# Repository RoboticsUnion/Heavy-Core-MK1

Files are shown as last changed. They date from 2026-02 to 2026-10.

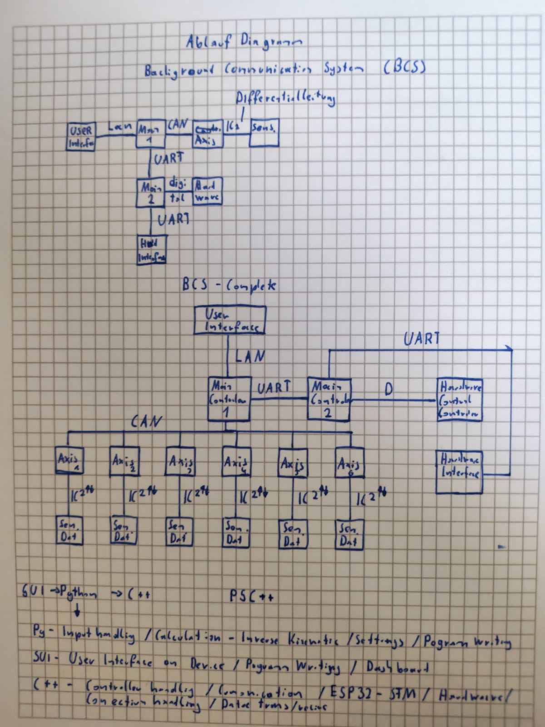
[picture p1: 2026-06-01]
electronic _engineering/BackgroundCommunicationSystem_ConceptDrwing.JPEG

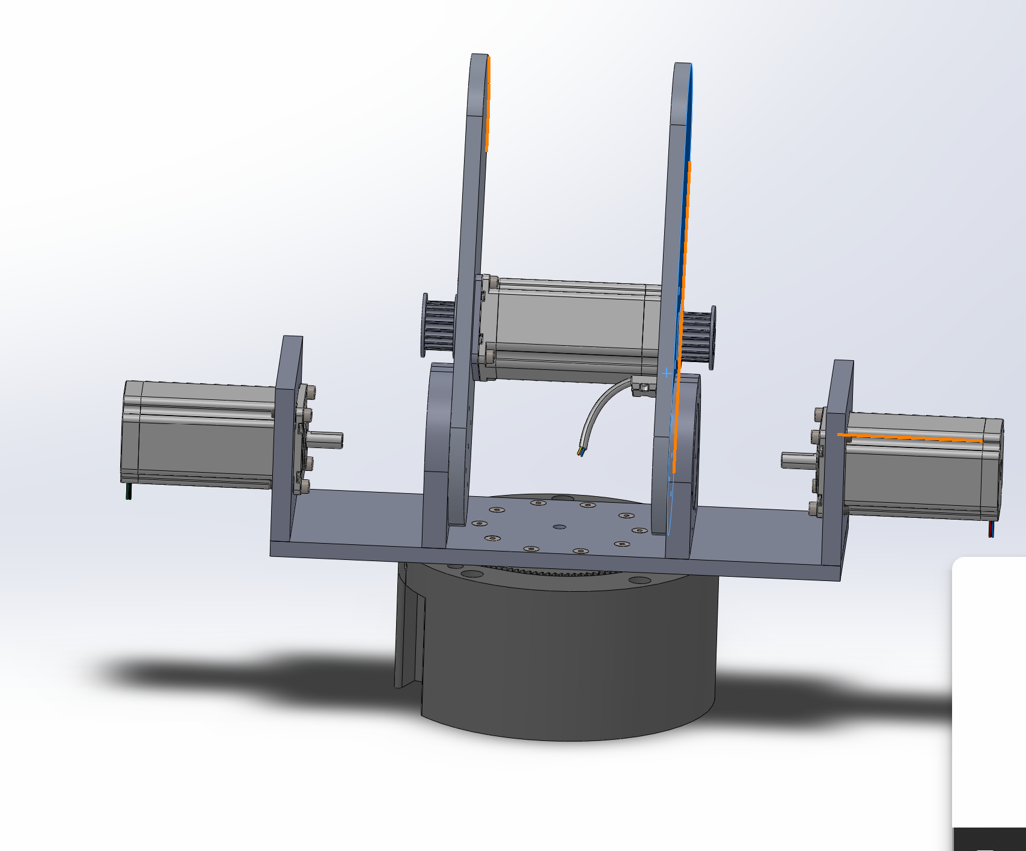
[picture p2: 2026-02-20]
docs/Images/ArmAssmb_Img1.png

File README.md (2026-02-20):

# Heavy-Core-MK1
Heavy-Core-MK1 is the development of a modular robotic arm platform.
The goal is to create a scalable, affordable robotics ecosystem where hardware and software are engineered together from the ground up.

The first two axes have already been designed, printed, assembled, and successfully tested. In parallel,
we are developing our own control software for precise motion control.

# Our Vision:

We aim to build a 6 DOF robitic arm that:
  - Is upgradeable with interchangeable end-effectors
  - Is structurally optimized for strength-to-weight efficiency
  - Includes a custom-developed control software
  - Allows future automation features
  - Serves as a platform for robotics development

# Custom Control Software

Our robotic arm will not rely solely on position control.
We are developing a control application that will include: 
  - Real-Time position feedback
  - Inverse kinematics calculations
  - Intuitive controls
  - Integrated arm simulation to prevent collisions or overload situations
  - Expandable architecture for future features

# Current Development Status

Completed:
  - Torque calculations
  - CAD design of Axis 1 and 2
  - Stepper motor integration
  - First tests of the custom designed Gearboxes
  - Functional test of both Axis

In Progress:
  - Development of remaining Axis
  - Gearbox optimization
  - Software development
  - Control hardware integration

# Preliminary Technical Specifications
- Target DOF: 6 DOF
- currently functional: 2 DOF
- Actuators: Stepper motors
- Structure: Aluminum & PLA (Stronger 3D-printed material planned)
- Control system: Arduino & ESP32 based
- Sofware: Custom standalone desktop or mobile application

# Development Roadmap

| Phase | Description | Target |

| MK1 Alpha | 2 DOF mechanical validation, first project showcase | Completed |

| MK1 Beta | 4-6 DOF mechanical prototype | Q3 2026 (estimated) |

| MK1 Software Alpha | Basic motion control & UI | Q3 2026 |

| MK1 Integrated Demo | Hardware + software functional for demonstration | Q1 2027 (January, HTL Open house) |

| MK1 Full Prototype | Fully functional 6 DOF with software improvements | Post Open House (future milestone) |

# Why this project stands out

Heavy-Core is more than a 3D-printed robotic arm.
It is the foundation for a modular robotics ecosystem that is mostly custom designed.

Mechanical engineering, electronics and software development are 
combined in one unified system, driven by the abition and passion of young engineers.

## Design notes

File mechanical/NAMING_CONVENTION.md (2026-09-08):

# CAD-Files Naming Convention

Each CAD-File is named according to our Naming Convention. This allows us to have relativly compact, but meaningfull names.

NamingCon_Example

The file name contains following components:
   - the project name,
   - the subassembly, the file is contained in,
   - a rising part number, starting at 001 for every subassembly (not used for assemblies),
   - the category of the part,
   - the version number

NOTE: In some cases it is possible to put a small clarification (1-2 words) between the part category and version number

# List of available abbreviations

  Project Name:
  - HC1 = HeavyCore MK1 

  Subassembly:
  - BA = Base
  - SH = Shoulder
  - EB = Elbow
  - UPA = Upper arm
  - WR = Wrist
  - GRP = Gripper
  
  Part Category:
  - MT = Mount
  - GR = Gear
  - PLT = Plate
  - SPC = Spacer
  - PIN = Pin
  - HUB = Hub
  - SHAFT = Shaft
  - BRCKT = Bracket

  Exeptions:
  - CM = Common ( this is used for parts that are contained in several subassemblies, but are created for this project and not sourced from outside)
  - ASM = Assembly

# Clarifications

- Plate = mostly used for flat plates that are used as structural elements.
- Mount = used for parts that hold, support, or attach components in place.
- Bracket = used for structural parts that are used to connect, support, or secure components, often at an angle.

Not every subassembly that may be contained in this project has its own abreviation. The prject is divided into 6 subassemblies, one for each axis,
and the common folder, wich is a bit of an exeption. Smaller subassemblies within one of the declared subassemblies must not be specificly labeled in the file names.
However, a new folder can be created to organize files.

NamingCon_Example1

Example Assembly File Name:

NamingCon_Example2

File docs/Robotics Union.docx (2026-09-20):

Robotics Union

Junior Company David Dovjak, Eder Samuel

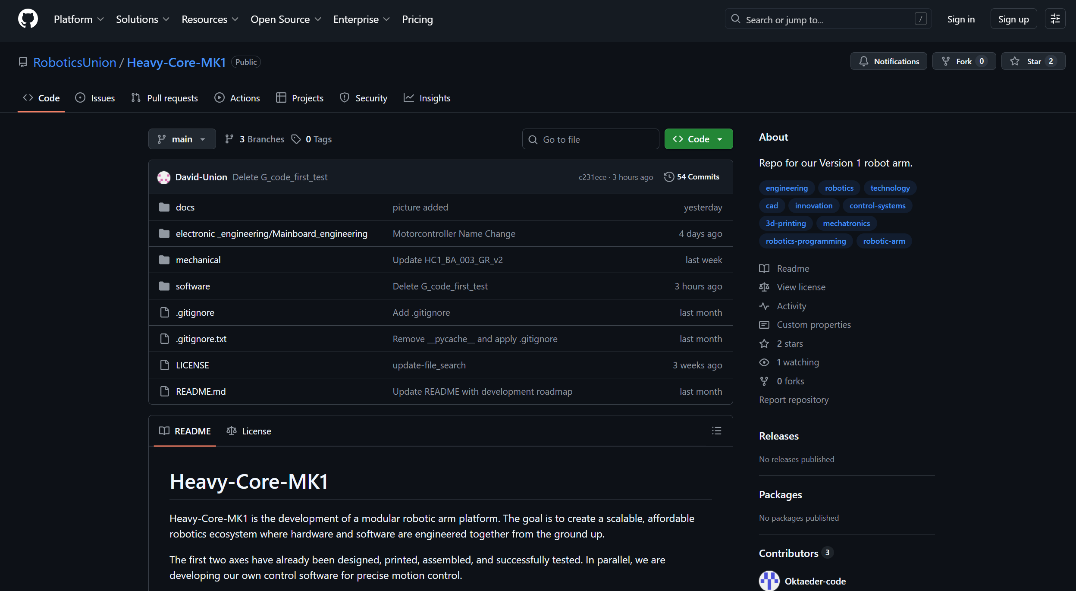
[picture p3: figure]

GitHub

Unser Hauptprojekt kann unter folgendem Link auf GitHub geöffnet werden: GitHub (https://github.com/RoboticsUnion/Heavy-Core-MK1)

Auf GitHub werden unsere Bauteile und Codes täglich geupdatet und ausgearbeitet. Dort gibt es auch direkt eine Übersicht, bzw. kann der Code getestet und die Bauteile als CAD-Datei geöffnet werden.

Code:

Der Code wird in C++ und Python geschrieben.

Bauteile:

Die Bauteile wurden in Fusion bearbeitet und seit neusten wechselten wir auf SolidWorks

Aufteilung:

David Dovjak – Code, Elektronik und Konstruktion der Werkzeugwechselstation

Eder Samuel – Konstruktion des Roboter Armes, Berechnung

GitHub Übersicht (siehe Link)

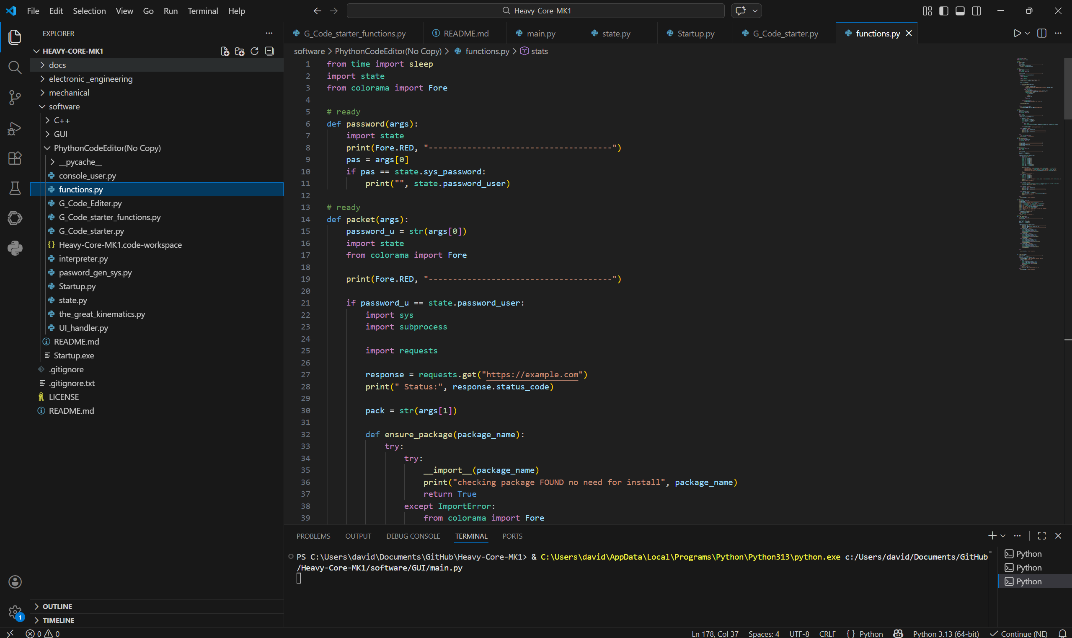
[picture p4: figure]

VS – Visual Studio Code

Alle Programme werden in Visual Studio Code geschrieben und bearbeitet. Python Code in der frontend und im backend; der C++ Teil ist für die Steuerung der Microcontroller. Vorher wurde in Py Charm gearbeitet, aber durch bessere Bearbeitungsmöglichkeiten haben wir auf VS gewechselt.

VS (Visual Studio Code): Ausschnitt der Programmierung

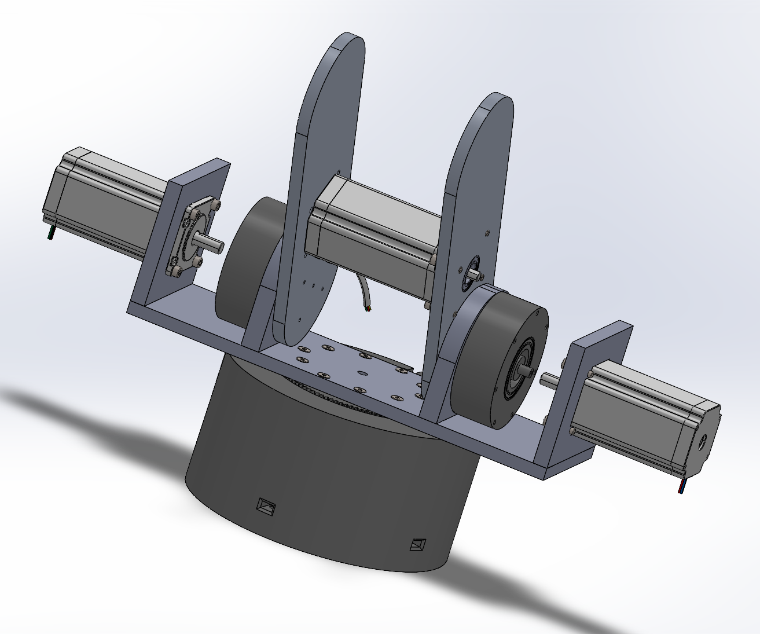
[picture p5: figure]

Konstruktion

CAD-Baugruppe des Roboterarmes (derzeitiger Stand)

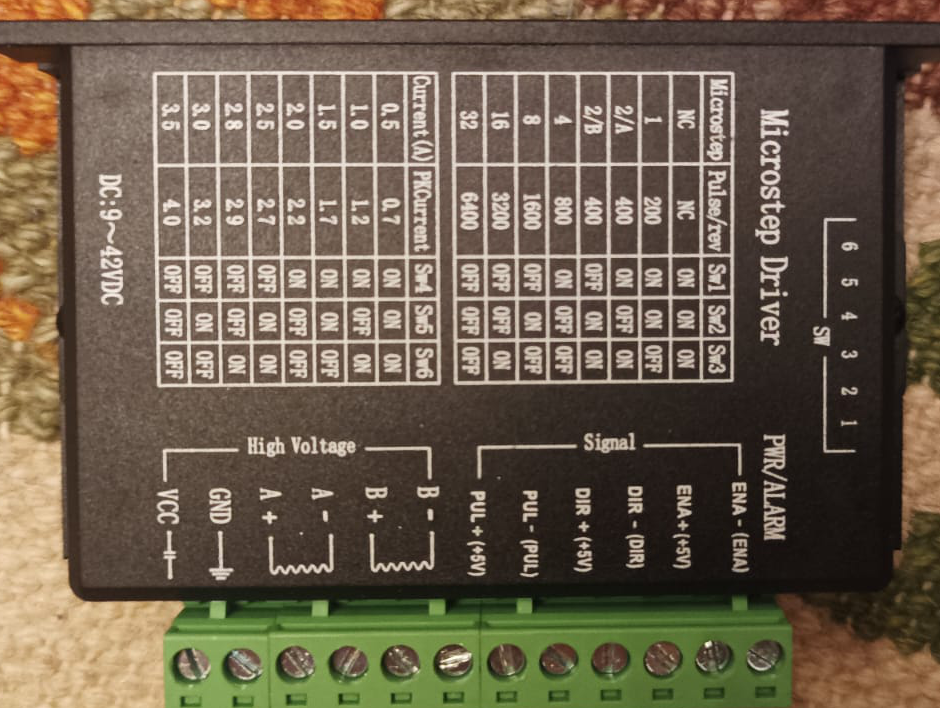
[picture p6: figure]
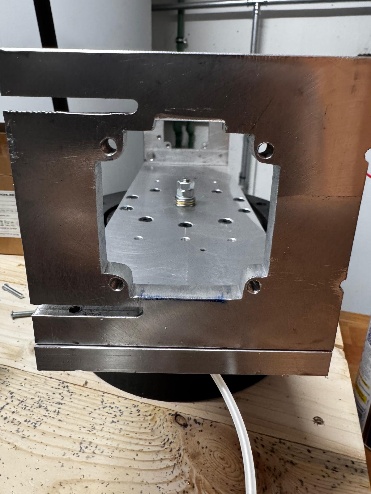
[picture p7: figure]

Motorcontroller TB6600

Aufbau: Motorhalterung 2. Achse

Aktueller Stand

Aktuell sind die ersten 2 Achsen fertig konstruiert, sowie selbst gefräst und zusammengebaut. Es wird gerade an der 3. Achse mit Riemenantrieb gearbeitet. Im fertigen Zustand soll der Roboterarm 6 Achsen haben, und einen Tool-Kopf der in x- und y-Richtung bewegt werden kann. Wir wollen damit einen Roboter bauen, der alle Aufgaben in der Industrie erledigen kann.

Der Arm hat eine maximale Hebekraft von bis zu circa 4 kg und durch unsere eigens erfundene Steuerung sollte er eine genaue und präzise Ausführung haben.

Getriebe:

Eigens designte cycloiden Getriebe, die eine starke Übersetzung liefern.

Motoren:

Wir verwenden Stepper Motoren der Ausführung Nema 17 und Nema 12 die mit einen TB6600 angesteuert werden.

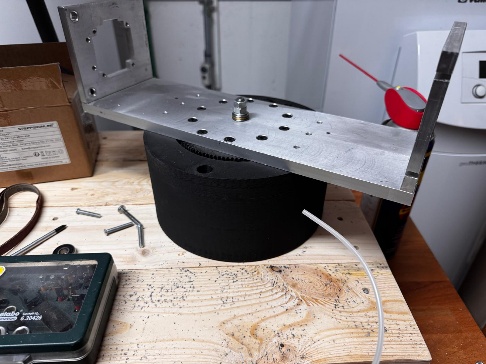
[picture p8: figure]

Aufbau: 1. und 2. Achse

Ziele

Wir haben bis jetzt schon ein großes Ziel erledigt: wir wurden seit Anfang des Projektes finanziell und logisch unterstützt, deswegen stellten wir am Infotag der HTBLVA Ferlach unseren Roboterarm aus und wir bekamen sehr viel gutes Feedback.

Für die Zukunft:

Fertigstellung des Armes in der Software SolidWorks und herstellen der benötigten Teile aus Aluminium und gehärtetem PLA für 3D-Drucker.

Software Fertigstellung GUI-Oberfläche des Hauptprogrammes. Dazu werden wir in Zukunft eine Kamera und einen LiDAR Sensor anbauen. Die zwei Komponenten werden von KI verarbeitet und es werden dann Funktionen zur Verfügung gestellt werden das per KI-Funktionen wie „Nimm den Blauen Würfel und lege ihn auf die Blau Fläche“ ausgeführt werden können.

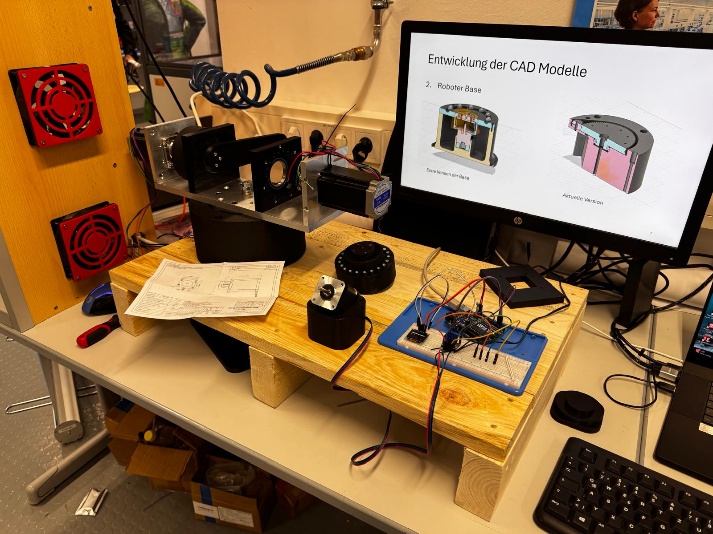
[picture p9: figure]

Auststellung am Infotag der HTBLVA Ferlach

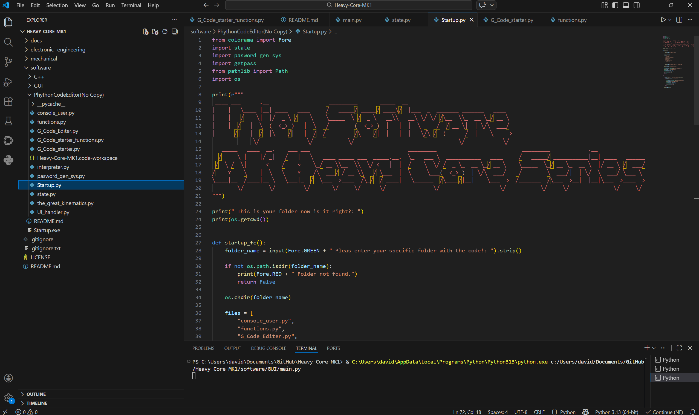
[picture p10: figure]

VS (Visual Studio Code): Ausschnitt der Programmierung

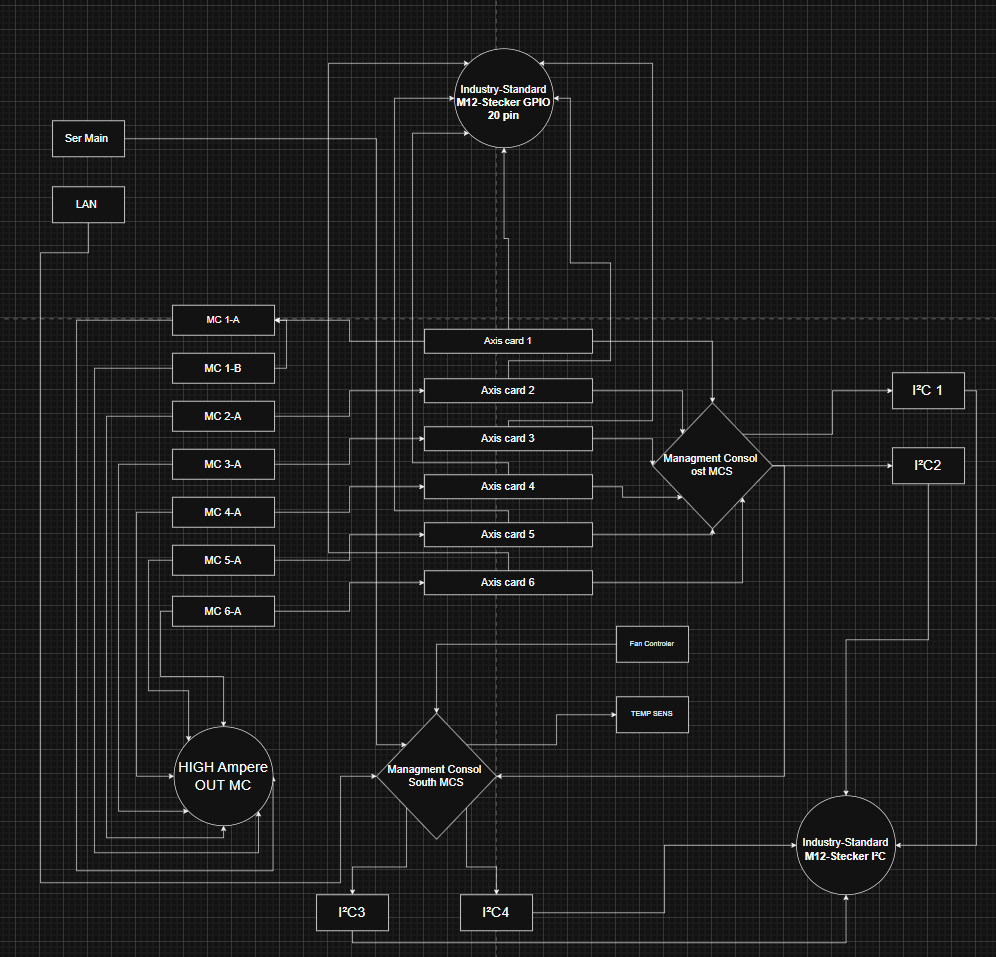
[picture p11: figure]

Logischer Aufbau von der Steuerungseinheit

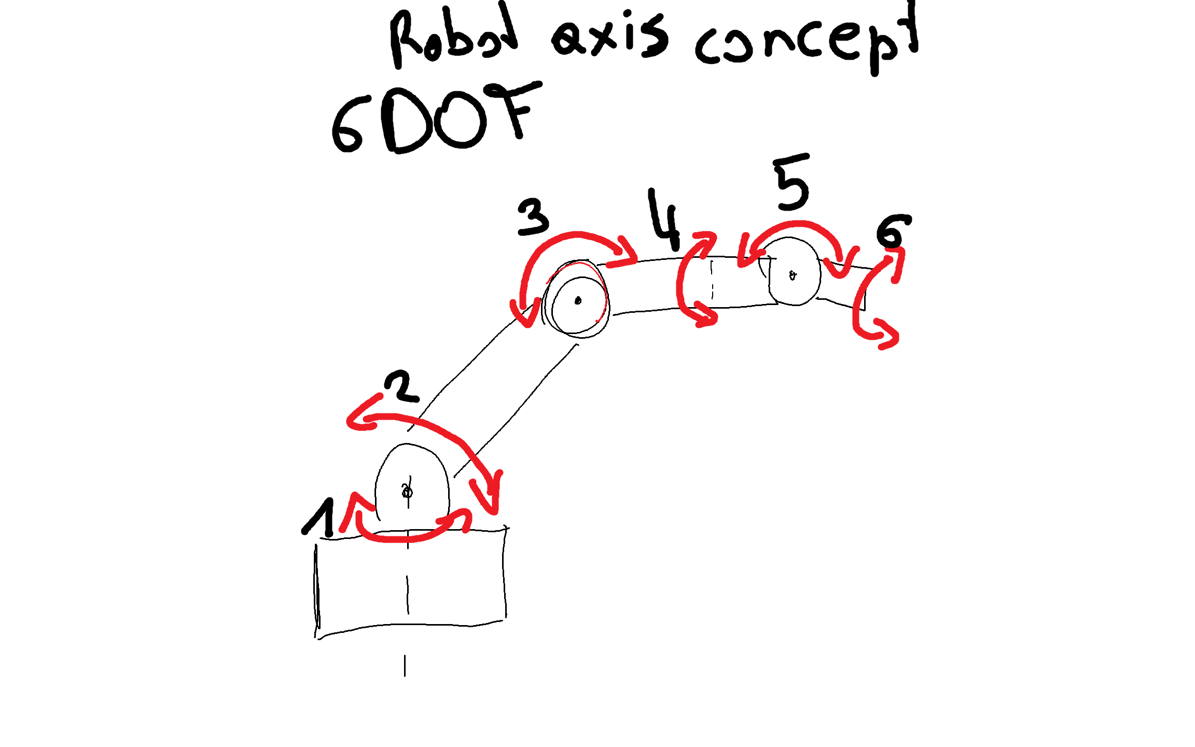
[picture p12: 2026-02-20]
docs/drawings/RobotAxisConcept.png

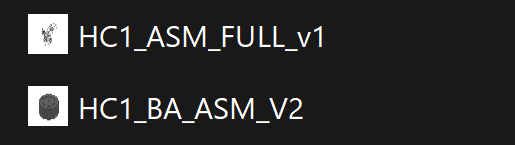
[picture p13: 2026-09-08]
docs/Images/NamingCon_Example2.png

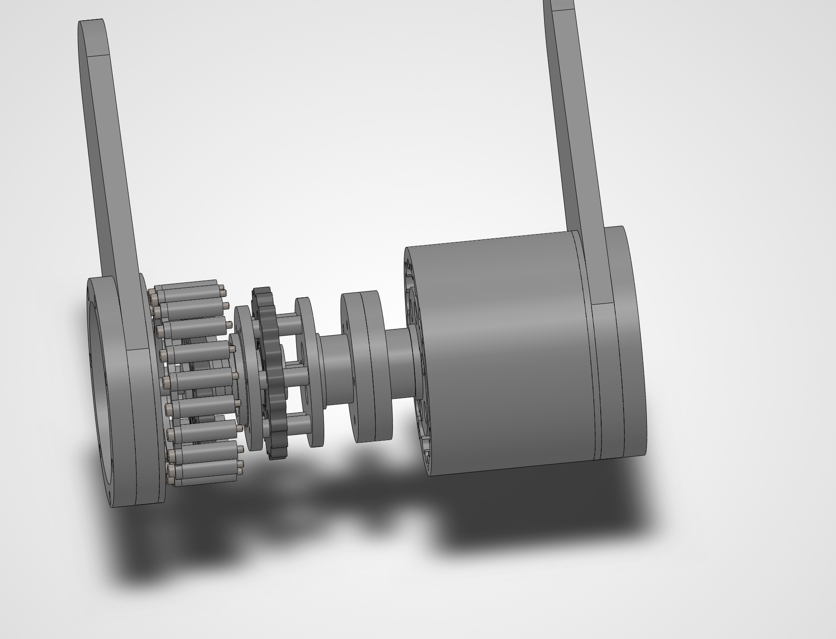
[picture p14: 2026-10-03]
docs/Images/Screenshot 2026-10-02 091949.png

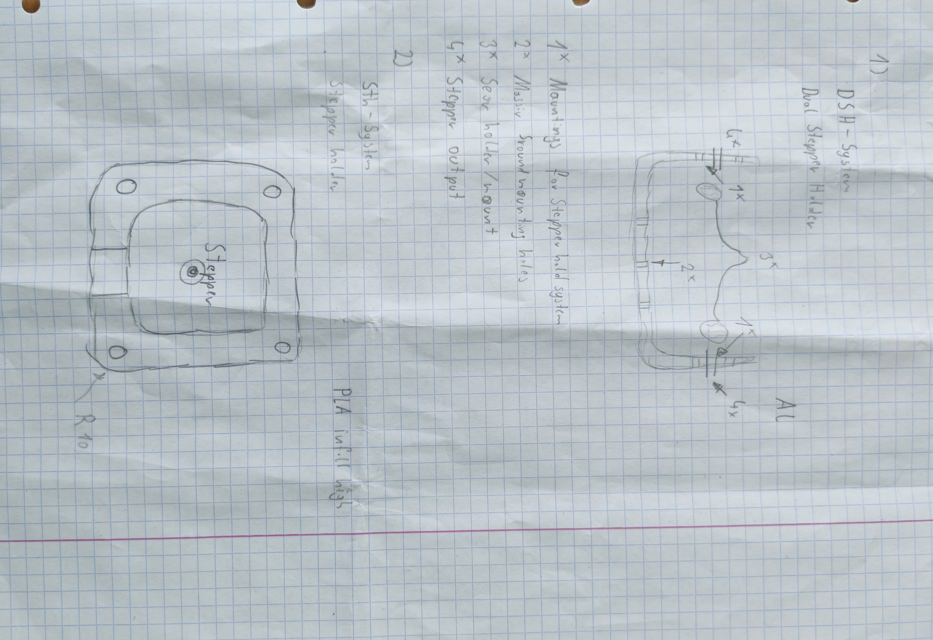
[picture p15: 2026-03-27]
docs/drawings/IMG_20260327_110558_edit_99301896493837.jpg

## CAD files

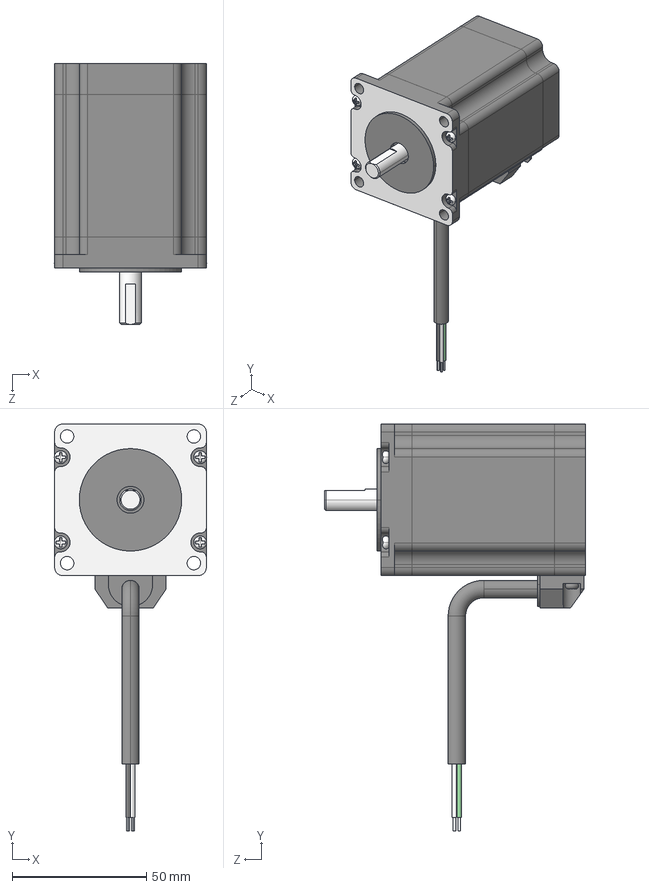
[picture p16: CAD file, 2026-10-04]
mechanical/assets/steppermotor/23HS30-2694S-Nema23SingleS_1.85nm.STEP
56.7 x 151.4 x 97.0 mm

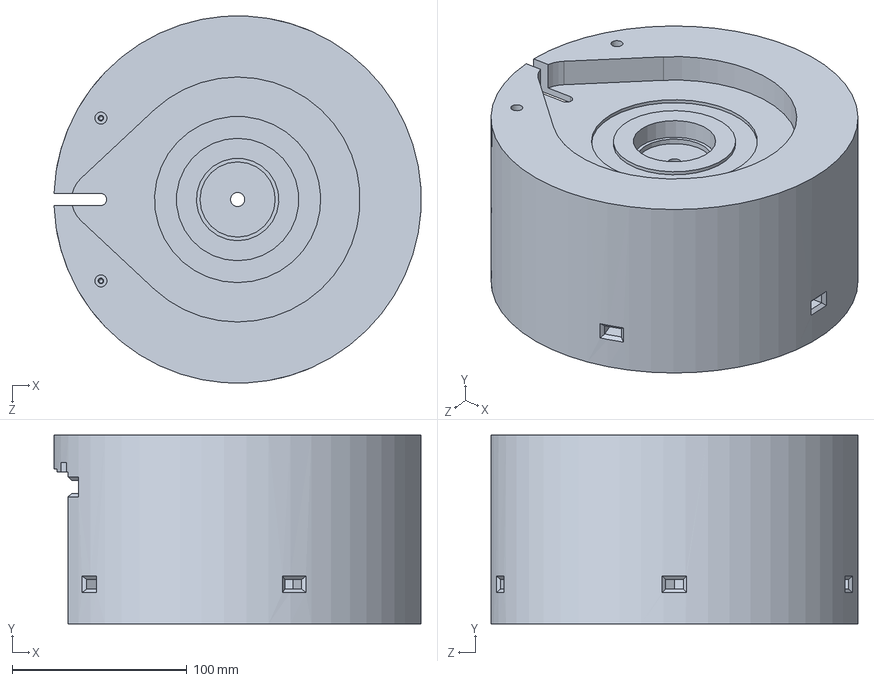
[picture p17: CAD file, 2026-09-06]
mechanical/cad/base/HC1_BA_001_MT_v2.SLDPRT
209.7 x 108.0 x 209.8 mm

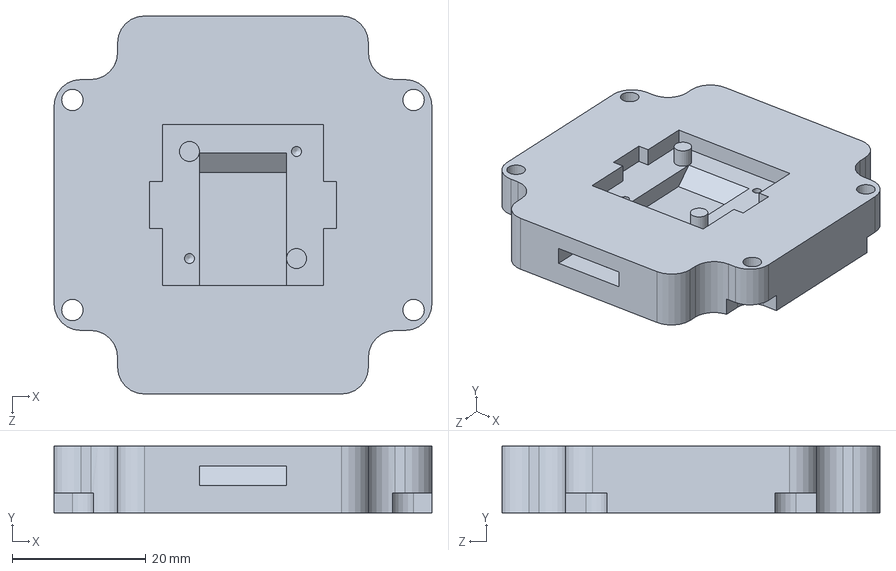
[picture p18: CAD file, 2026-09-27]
mechanical/cad/common/encoder_mounts/HC1_CM_001_MT_ENCODER_Nema23_v1.SLDPRT
56.5 x 10.0 x 56.5 mm

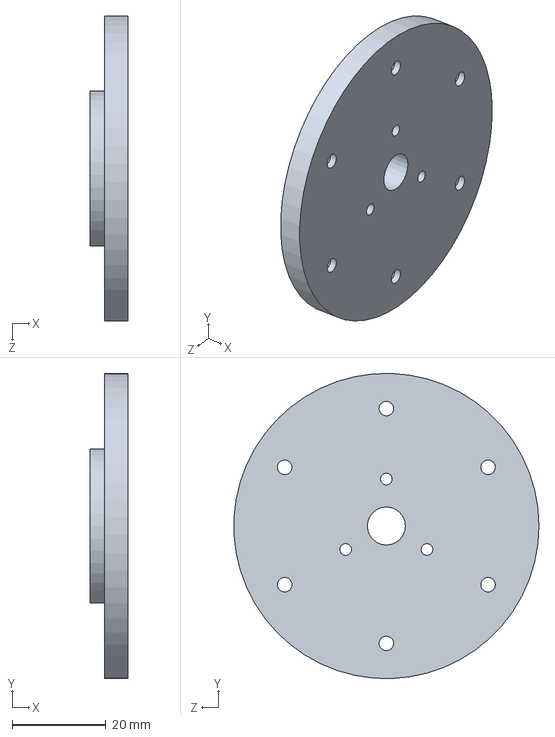
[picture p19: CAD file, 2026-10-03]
mechanical/cad/ellbow/CycloidalDrive/HC1_EB_005_MT_staticPins_v2.SLDPRT
8.00 x 65.0 x 64.9 mm

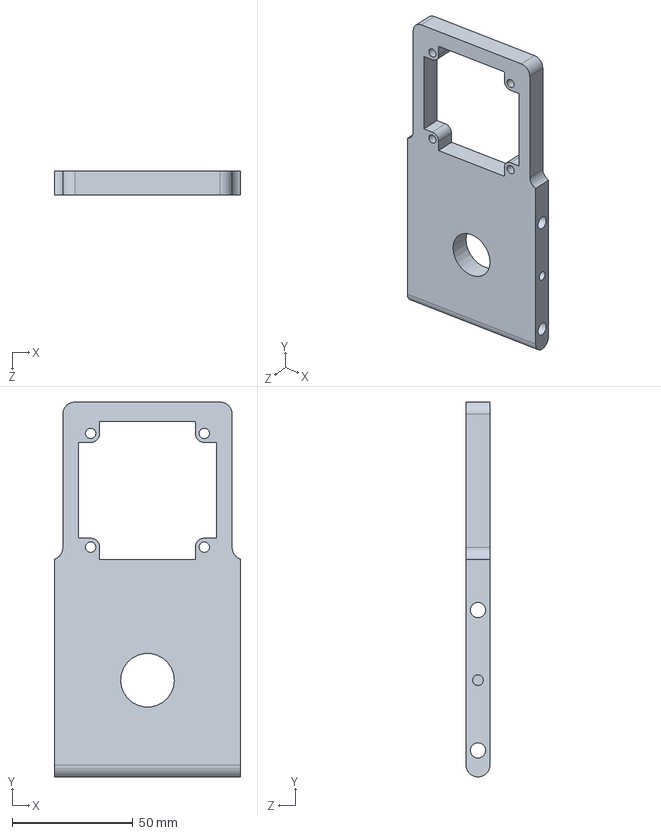
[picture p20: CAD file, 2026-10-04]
mechanical/cad/ellbow/HC_EB_13_MT_stepper_v1.SLDPRT
77.0 x 155.0 x 10.0 mm

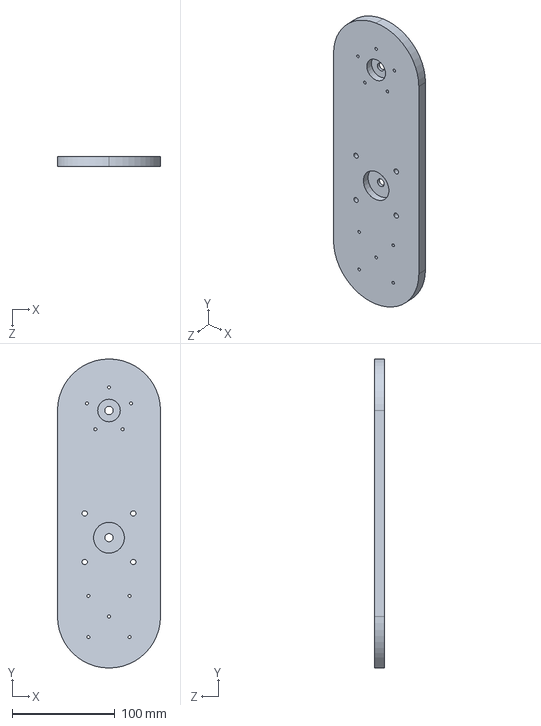
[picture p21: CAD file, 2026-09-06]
mechanical/cad/shoulder/HC1_SH_006_PLT_Axis_v1.SLDPRT
100.0 x 300.0 x 10.0 mm

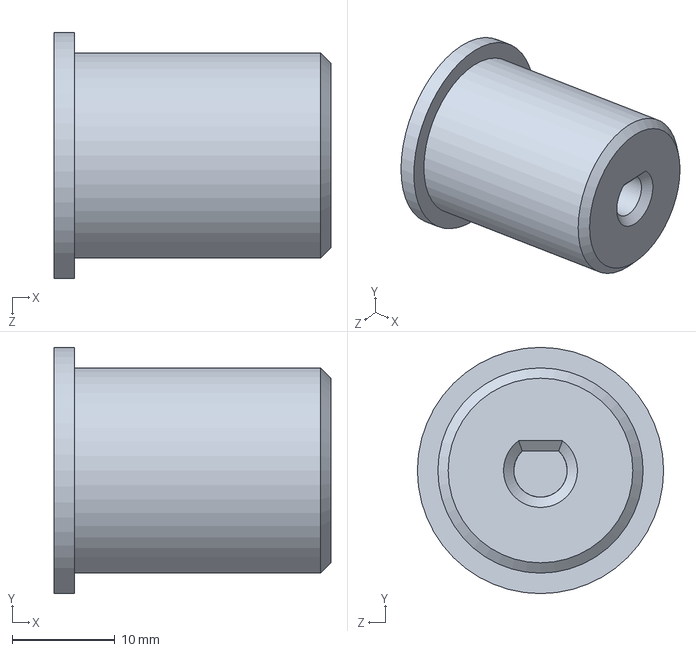
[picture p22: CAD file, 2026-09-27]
mechanical/cad/test_dev_parts/Cycloidal_input_Nema17.SLDPRT
27.0 x 24.0 x 24.0 mm

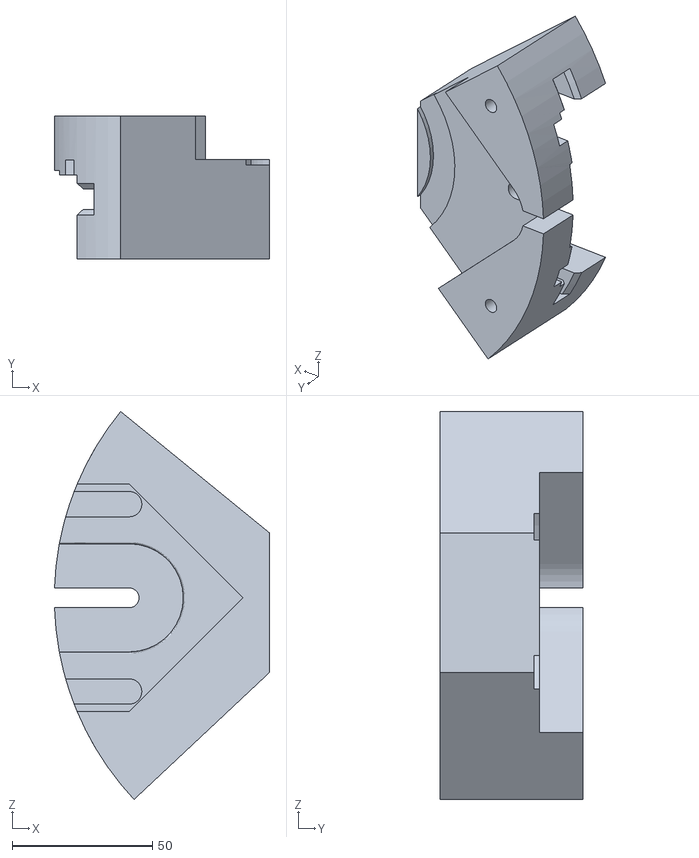
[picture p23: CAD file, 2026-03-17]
mechanical/stl/base/HC1_BA_001_MT_Ausschnitt.STL
76.6 x 51.0 x 138.2

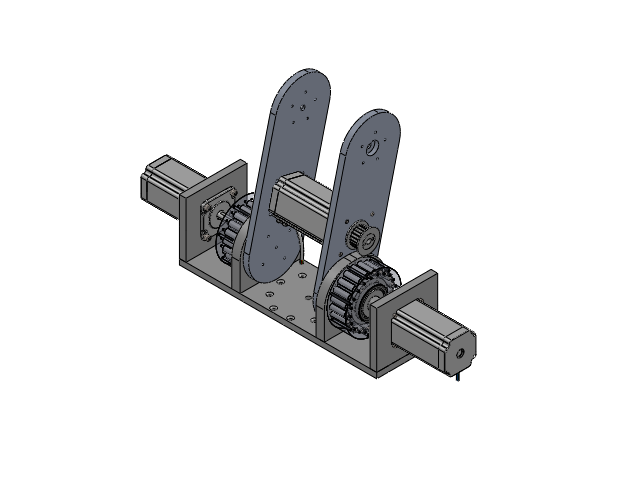
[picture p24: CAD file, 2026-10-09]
mechanical/assemblies/HC1_SH_ASM_v1.SLDASM
HC1_SH_001_PLT_v1
HC1_SH_002_MT_Motor_v1 x 2
HC1_SH_003_MT_Gearbox_v2 x 2
23HE45-4204S-Nema23SingleS.step x 2
69032RS Inner ring.stp x 2
69032RS Outer ring.stp x 2
69032RS Ball.stp x 22
69032RS Seal.stp x 4
6808ZZ Inner ring.stp x 2
6808ZZ Outer ring.stp x 2
6808ZZ Ball.stp x 42
6808ZZ Shield.stp x 4
HC1_SH_006_PLT_Axis_v1 x 2
HC1_SH_007_SPC_Motor_v1
HTD5M-Pully-20t x 2
HTD5M-Pully-20t-BeltGuard x 4
socket_head_cap_screw_M5x20 x 12
HC1_SH_008_MT_housing_v1 x 2
HC1_SH_011_PIN_static_v1 x 42
socket head cap screw_iso x 42
HC1_SH_009_MT_dynamicPin_v2 x 2
HC1_SH_012_PIN_dynamic_v2 x 12
HC1_SH_010_MT_output_v2 x 2
HC1_SH_HUB_input_v2 x 2
HC1_SH_013_HUB_excentr_v2 x 2
HC1_SH_014_HUB_v1 x 2
HC1_EB_013_PLT_Cycloidal1_v1 x 2
HC1_EB_014_PLT_Cycloidal2_v1 x 2
68042RS Inner ring x 8
68042RS Outer ring x 8
68042RS Ball x 104
68042RS Seal x 16
6808ZZ Inner ring x 2
6808ZZ Outer ring x 2
6808ZZ Ball x 42
6808ZZ Shield x 4
HC1_SH_015_SPC_Pins_v1 x 2
countersunk_flat_head_cross_recess_screw_M3x30 x 12
23HS45-4204D-Nema23DoubeS.step

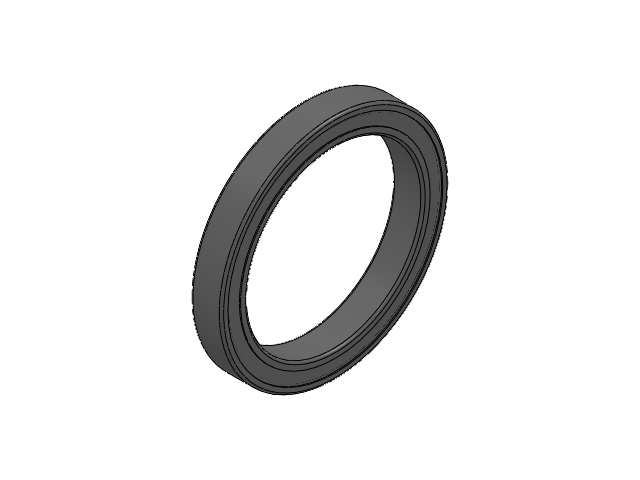
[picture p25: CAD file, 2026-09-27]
mechanical/assets/bearings/6808ZZ/6808ZZ.SLDASM
6808ZZ Inner ring
6808ZZ Outer ring
6808ZZ Ball x 21
6808ZZ Shield x 2

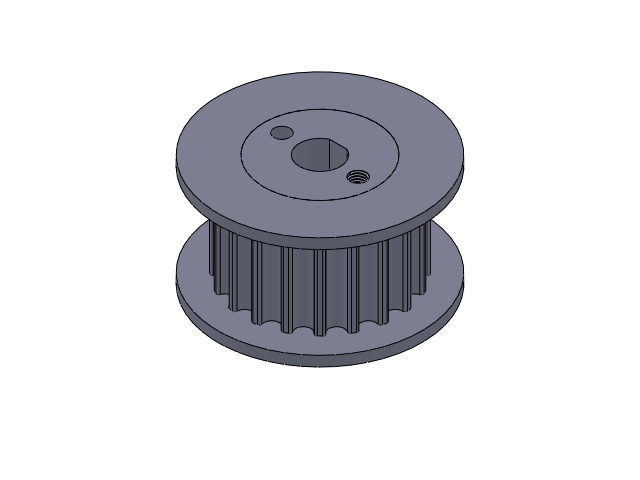
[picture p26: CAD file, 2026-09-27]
mechanical/assets/beltdrive/HTD5M_Pully_20t_Asmb_v1.SLDASM
HTD5M-Pully-20t
HTD5M-Pully-20t-BeltGuard x 2

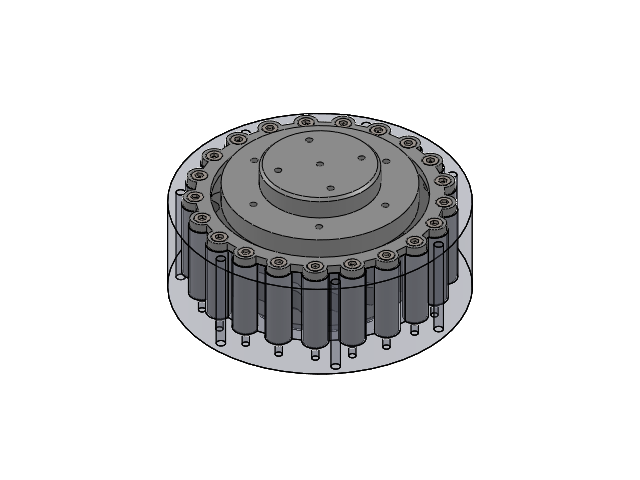
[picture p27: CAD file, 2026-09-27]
mechanical/cad/shoulder/CycloidalDrive/HC1_ASM_cycloidalDrive.SLDASM
HC1_SH_008_MT_housing_v1
HC1_SH_011_PIN_static_v1 x 21
socket head cap screw_iso x 21
HC1_SH_009_MT_dynamicPin_v2
HC1_SH_012_PIN_dynamic_v2 x 6
HC1_SH_010_MT_output_v2
HC1_SH_HUB_input_v2
HC1_SH_013_HUB_excentr_v2
HC1_SH_014_HUB_v1
HC1_EB_013_PLT_Cycloidal1_v1
HC1_EB_014_PLT_Cycloidal2_v1
68042RS Inner ring x 4
68042RS Outer ring x 4
68042RS Ball x 52
68042RS Seal x 8
6808ZZ Inner ring
6808ZZ Outer ring
6808ZZ Ball x 21
6808ZZ Shield x 2
HC1_SH_015_SPC_Pins_v1
countersunk_flat_head_cross_recess_screw_M3x30 x 6

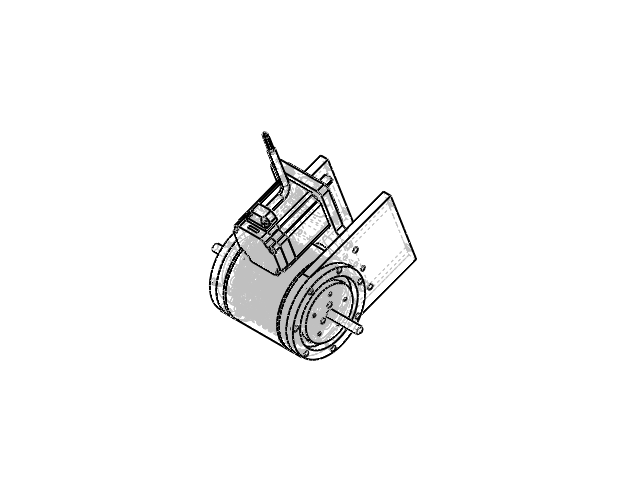
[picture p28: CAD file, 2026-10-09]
mechanical/assemblies/HC1_EB_ASM_v1.SLDASM
HC1_EB_001_BRCKT_Bearing_v2 x 2
32906-H.step x 2
HC1_EB_003_PLT_Axisplt_v1 x 2
HC1_EB_002_SPC_v1 x 2
HC1_EB_004_PLT_v1 x 2
HC1_EB_005_MT_staticPins_v2 x 2
HC1_EB_006_MT_housing_v1
6808ZZ Inner ring.stp
6808ZZ Outer ring.stp
6808ZZ Ball.stp x 21
6808ZZ Shield.stp x 2
HC1_EB_009_MT_staticPins2_v1 x 2
HC1_EB_010_PIN_static_v1 x 12
HC1_EB_011_SPC_bearings_v1
HC1_EB_012_SHAFT_v1
HC1_EB_013_HUB_v1 x 2
HC1_EB_014_HUB_excntr1_v1
HC1_EB_015_HUB_excntr2_v1
HC1_EB_007_PLT_Cycloidal1_v1
68042RS Inner ring.stp x 4
68042RS Outer ring.stp x 4
68042RS Ball.stp x 52
68042RS Seal.stp x 8
HC1_EB_008_PLT_Cycloidal2_v1
HC1_EB_016_PIN_moving_v1 x 42
socket_head_cap_screw_M3x30 x 42
HC1_EB_017_SPC_Pins_v1 x 2
HC_EB_13_MT_stepper_v1
23HS30-2694S-Nema23SingleS_1.85nm.step
HC1_CM_001_MT_ENCODER_Nema23_v1

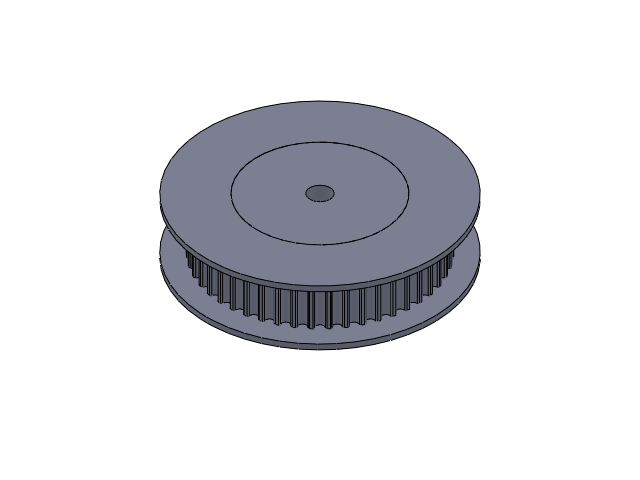
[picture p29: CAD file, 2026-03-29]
mechanical/assets/beltdrive/HTD5M_Pully_48t_Asmb_v1.SLDASM
HTD5M_Pully_48t_v1
HTD5M_Pully_48t_BeltGuard_v1 x 2

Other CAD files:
software/main_core/C++/Main_runtime/main.obj
mechanical/assemblies/HC1_ASM_FULL_v1.SLDASM
software/main_core/C++/main.obj
mechanical/assemblies/HC1_BA_ASM_V2.SLDASM
mechanical/assets/bearings/32906-H.step
mechanical/assets/bearings/608.stp
mechanical/assets/bearings/68042RS.stp
mechanical/assets/bearings/68042RS/68042RS Ball.SLDPRT
mechanical/assets/bearings/68042RS/68042RS Inner ring.SLDPRT
mechanical/assets/bearings/68042RS/68042RS Outer ring.SLDPRT
mechanical/assets/bearings/68042RS/68042RS Seal.SLDPRT
mechanical/assets/bearings/68042RS/68042RS.SLDASM
mechanical/assets/bearings/6808ZZ.stp
mechanical/assets/bearings/6808ZZ/6808ZZ Ball.SLDPRT
mechanical/assets/bearings/6808ZZ/6808ZZ Inner ring.SLDPRT
mechanical/assets/bearings/6808ZZ/6808ZZ Outer ring.SLDPRT
mechanical/assets/bearings/6808ZZ/6808ZZ Shield.SLDPRT
mechanical/assets/bearings/69032RS.stp
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

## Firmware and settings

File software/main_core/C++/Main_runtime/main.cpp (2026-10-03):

#include "..\Terminal\Terminal-OUT\Terminal-OUT.hpp" 

#include "../ansi_color_chart/ansi_color_chart.hpp"


#include <iostream>

std::string example = "example_text";

int main() {
    TerminalOUT terminal;
    terminal.terminal_standard_output();
    terminal.terminal_custom_output("\n Custom_output_example\n", ansi_color_chart::blue);
    terminal.terminal_custom_output(example, ansi_color_chart::green);
    terminal.load_error_message("../Terminal/Terminal-IN/error_list.txt");
    std::string error = terminal.terminal_error_output("example_error_reason");
    std::cout << "\n" + error;

}

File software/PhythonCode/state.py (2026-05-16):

# state.py

password_user = None
sys_password = None

console_user_running = True
g_code_editor_running = False
g_code_starter_running = False


file = None

# state.py

execute_live = None #set to False when in use

commands_text = """
ALL COMMANDS OF THE SOFTWARE

MAIN CONSOLE COMMANDS

help
Shows the main help page.
Usage:
help

exit
Closes the main console and stops the software.
Usage:
exit

pas
Shows the user password, but only if the generated system password is correct.
The system password is printed at startup.
Usage:
pas <system_password>

pip
Checks if a Python package exists. If it is missing, the software tries to install it with pip.
Usage:
pip <user_password> <package_name>
Example:
pip mypass colorama

ser
Serial configuration command.
Usage for setting serial:
ser set <user_password> <port> <baud_rate> <timeout>
Example:
ser set mypass COM3 9600 1

Usage for serial help:
ser help <user_password>

cal
Calibration command for robot arm values.

Manual calibration:
cal man <user_password> <l1> <l2> <l3> <r1> <r2> <w1> <w2> <w3> <tool_x> <tool_y>
Example:
cal man mypass 100 120 80 0 0 45 45 45 0 0

Automatic basic length calibration:
cal auto <user_password> <l1> <l2> <l3>
Example:
cal auto mypass 100 120 80

Tool length:
cal tl <user_password> <tool_length>
Example:
cal tl mypass 50

Delete all calibration values:
cal dump <user_password>

Calibration help:
cal help <user_password>

stat
Shows current statistics and stored state values:
terminal lines, arm lengths, rotation values, angle values, tool values and selected compiler file.
Usage:
stat

g-e
Opens the G-Code editor functions.
Usage:
g-e <mode> <user_password>

Modes:
g-e help <user_password>
Shows editor help.

g-e make <user_password>
Creates a new empty G-Code file. The program asks for the file name.

g-e write <user_password>
Opens write mode. The program asks for the file name, then you write line 1, line 2, line 3, etc.
Type exit inside the writer to return to the main console.

g-e edit <user_password>
Opens edit mode for an existing file.
Inside edit mode:
show = display the file with line numbers
edit = edit one selected line
exit = return to main console

g-e delete <user_password>
Deletes a selected file. The program asks for the file name.

g-s
Starts the G-Code starter section.
Usage:
g-s <user_password>
After that the program asks:
Do you want to continue? (Y/n)
Enter Y to start, n to cancel.

helpGUI
Opens the manual GUI window.
Usage:
helpGUI <user_password>

clock
Shows a live clock in the console.
Hold q to close the clock.
Usage:
clock <user_password>


G-CODE STARTER COMMANDS

These commands are only available after starting the starter with:
g-s <user_password>

exit
Leaves the G-Code starter and returns to the main console.
Usage:
exit

file
Sets the G-Code file that should be used by the compiler.
Usage:
file <user_password> <filename>
Example:
file mypass test.gcode

compile
Checks the selected G-Code file for syntax errors.
You must set a file first with the file command.
Usage:
compile <user_password>

recive
Starts TCP receive mode and saves received data into buffer.txt.
Data is split by semicolons. Every part before a semicolon becomes one line in buffer.txt.
Usage:
recive <user_password> <host> <port>
Example:
recive mypass 0.0.0.0 5000

recive_live
Starts live receive mode.
This function exists in the code but is marked as unfinished.
Use carefully.
Usage:
recive_live <user_password> <host> <port>
Example:
recive_live mypass 0.0.0.0 5000

help
Shows the G-Code starter help text.
Usage:
help <user_password>


SUPPORTED G-CODE COMMANDS IN THE COMPILER

The compiler currently accepts these G-Code commands:

G0
Fast movement to a position.
Allowed parameters:
X, Y, Z
Example:
G0 X100 Y50 Z20

G1
Movement to a position with feed/speed value.
Allowed parameters:
X, Y, Z, F
Example:
G1 X100 Y50 Z20 F1500

G78
Special command with X, Y, feed and S value.
Allowed parameters:
X, Y, F, S
Example:
G78 X10 Y20 F500 S1

G-Code comments:
Text inside round brackets is ignored.
Example:
G0 X10 Y20 Z30 (this is a comment)

Everything after a semicolon is ignored by the compiler.
Example:
G1 X10 Y20 Z30 F1000 ; comment

Note:
The old help text mentions GD and G1-s, but these commands are not implemented in the current compiler command list.
"""


basic_text = """
HEAVY CORE MK1 CMD-CONTROL - BASIC OVERVIEW

This software is a command line control system for a robot arm.

Start the program with Startup.py.
At startup the program asks for the folder that contains the project files.
After that it generates a system password and asks the user for a user password.

The user password is needed for most control commands.
The system password can be used with the pas command to show the user password again.

Main workflow:
1. Start Startup.py.
2. Enter the project folder.
3. Enter your user password.
4. Use help to show the command overview.
5. Calibrate the robot arm with cal.
6. Create or edit G-Code with g-e.
7. Start the G-Code starter with g-s.
8. In the starter, select a file with file and check it with compile.

Important states:
console_user_running controls the main terminal.
g_code_editor_running controls the G-Code editor.
g_code_starter_running controls the G-Code starter.
state.file stores the selected G-Code file.
"""


help_text = """
HELP OVERVIEW

This project contains a terminal based robot arm control system.

Important files:
Startup.py starts the whole software.
console_user.py runs the main command input loop.
interpreter.py connects main console commands to their functions.
functions.py contains the main command functions.
G_Code_Editer.py contains file creation, writing, editing and deleting.
G_Code_starter.py runs the G-Code starter command loop.
G_Code_starter_functions.py contains compile, file selection and receive functions.
manual.py opens the graphical manual window.
state.py stores shared variables and manual texts.

Recommended use:
Start with Startup.py.
Use help to see the command list.
Use cal help to see calibration help.
Use g-e make or g-e write to create G-Code.
Use g-s to enter the G-Code starter.
Use file to select a G-Code file.
Use compile to check the selected file.

Safety:
Always calibrate the arm before movement or file execution.
Check all length, angle and tool values with stat.
Use the correct password for control commands.
Do not run unfinished live receive functions on real hardware without testing.
"""


gui_text = """
GUI BASIC OVERVIEW

The manual GUI is opened with:
helpGUI <user_password>

The window title is User Manual.
It contains five pages:

cmd-basics
Basic overview of the command control software.

cmd-commands
Complete command list for the main console, G-Code editor and G-Code starter.

cmd-help
General help and recommended workflow.

GUI-basics
Explanation of the manual GUI.

Content-Creation
Rules for creating or changing GUI content.
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

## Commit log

2026-01-19 Add README for CAD directory
2026-01-19 Add README for robot arm software
2026-01-19 Add README for Bill of Materials
    This README provides an overview of the bill of materials for the robot arm.
2026-01-19 added bom
    Added bom with first part, excel and csv file
    [bom-mk1.CSV, bom-mk1.xlsx]
2026-02-14 folder structure changed
    removed Folders
    [bom-mk1.CSV, bom-mk1.xlsx]
2026-02-14 Added Folder Structure
    Added a Folder for Mechanical Componets.
    With subfolders for cad, stl, drawings and assemblies.
2026-02-15 CAD Files added
    Added Solidworks Part Cad files to shoulder folder. Added assets folder with reusable standardized Components.
    [23HE45-4204S-Nema23SingleS.STEP, 23HS45-4204D-Nema23DoubeS.STEP, 6808ZZ.stp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]
2026-02-20 Images Added
    Images of the Axis Concept and the arm assembly added to docs/Images.
2026-02-20 Update README with project details and specifications
    Expanded project description, vision, current status, and specifications for the Heavy-Core-MK1 robotic arm.
2026-02-24 Remove __pycache__ and apply .gitignore
    [32906-H.step, HC1_BA_001_MT_v1.step, HC1_BA_003_GR_v1.step]
2026-03-06 Added Bearing .stp
    Added Bearing models:
    608
    7095
    [608.stp, as7095.stp, axk7095.stp]
2026-03-06 Base Rework + Asembly
    New Base fixture, added Axial Bearing, new motor fixture. Stepper Motor encoder will be added next.
    [HC1_BA_001_MT_v1.SLDPRT, HC1_BA_001_MT_v1.step, HC1_BA_001_MT_v2.SLDPRT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]
2026-03-06 Added .stp for Nema23 76mm lenght
    [23HE30-2804S.STEP]
2026-03-17 STL Printing Test Files Added
    [HC1_BA_001_MT_Ausschnitt.STL, HC1_BA_004_MT_v1.STL]
2026-03-17 CAD Files Added
    Axis 1 & 2
    [HC1_BA_001_MT_v2.SLDPRT, HC1_BA_004_MT_v1.SLDPRT, HC1_BA_004_MT_v2.SLDPRT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]
2026-03-17 Arm Assembly
    Sub Assembly Base, Sub Assembly Shoulder, Arm Assembly
    [HC1_BA_ASM_V2.SLDASM, ZykloidenGetriebeV1.step]
2026-03-17 Update mainUI.py
    Exit Button erstellt
2026-03-19 Changed Size of Screw hole
    Part: Base
    [HC1_BA_001_MT_v1.SLDPRT, HC1_BA_001_MT_v2.SLDPRT, HC1_BA_001_MT_v2.STL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]
2026-03-21 Added AS5600 Encoder Mounts
    CAD and STL files for AS5600 Motor Encoder
    [HC1_BA_ASM_V2.SLDASM, HC1_CM_001_MT_ENCODER_Nema23_v1.SLDPRT, HC1_CM_001_MT_ENCODER_Nema23_v1.STL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]
2026-03-22 Update HC1_BA_003_GR_v2
    Changed the Screwhole
    [HC1_BA_003_GR_v2.SLDPRT]
2026-03-24 Motorcontroller Name Change
2026-03-29 HTD5M 48t pully cad added
    [HTD5M_Pully_48t_Asmb_v1.SLDASM, HTD5M_Pully_48t_BeltGuard_v1.SLDPRT, HTD5M_Pully_48t_v1.SLDPRT]
2026-03-30 Base Small change
    Changed the base so that a stepper with the encoder fits in.
    [HC1_BA_001_MT_v2.SLDPRT]
2026-04-05 Started Work on Ellbow joint
    [HC1_EB_001_BRCKT_Bearing_v1.SLDPRT, HC1_EB_002_SPC_v1.SLDPRT, HC1_EB_003_PLT_Axisplt_v1.SLDPRT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]
2026-04-10 Start of Ellbow Joint, CAD files added
    [HC1_EB_001_BRCKT_Bearing_v1.SLDPRT, HC1_EB_002_SPC_v1.SLDPRT, HC1_EB_003_PLT_Axisplt_v1.SLDPRT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]
2026-04-10 changes on the ASM
    [HC1_EB_ASM_v1.SLDASM]
2026-04-10 Created Drive Housing, smal changes
    [HC1_EB_002_SPC_v1.SLDPRT, HC1_EB_003_PLT_Axisplt_v1.SLDPRT, HC1_EB_004_PLT_v1.SLDPRT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]
2026-04-17 New Parts added
    Finished Output Pins, Holder. Created Spacer for Bearings (Middle), created drive Axle.
    [HC1_ASM_FULL_v1.SLDASM, HC1_BA_ASM_V2.SLDASM, HC1_EB_001_BRCKT_Bearing_v1.SLDPRT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]
2026-04-19 Added Excentric input shaft parts, minor changes
    added the parts for the excentric input shaft where the bearings with the cycloidal drive plates sit. Configuration with 2 Cycloidal plates. Updated Ellbow assembly.
    [68042RS.stp, HC1_ASM_FULL_v1.SLDASM, HC1_BA_ASM_V2.SLDASM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]
2026-04-23 update - g-s / new help text via GUI
    added save and live streaming of data from a Control pad and help/ updated help/ fixed bugs
    [G_Code_starter.py, G_Code_starter_functions.py, functions.py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]
2026-04-23 added spc plate for pins; finished v1
    Finished v1 of the joint. Not tested might still get changes
    [HC1_EB_006_MT_housing_v1.SLDPRT, HC1_EB_016_PIN_moving_v1.SLDPRT, HC1_EB_017_SPC_Pins_v1.SLDPRT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]
2026-04-26 added stl's, minor change pin mount
    changed the way the static pins are screwed to the pin mount. Stl: Static pin, drive housing.
    [HC1_EB_006_MT_housing_v1.STL, HC1_EB_009_MT_staticPins2_v1.SLDPRT, HC1_EB_010_PIN_static_v1.STL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]
2026-04-28 added srewholes for ellbow attachement
    [HC1_SH_006_PLT_Axis_v1.SLDPRT, HC1_SH_ASM_v1.SLDASM, HTD5M_Pully_20t_Asmb_v1.SLDASM]
2026-04-28 deleted files for branch merging
    [HC1_EB_001_BRCKT_Bearing_v1.SLDPRT, HC1_EB_002_SPC_v1.SLDPRT, HC1_EB_003_PLT_Axisplt_v1.SLDPRT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]
